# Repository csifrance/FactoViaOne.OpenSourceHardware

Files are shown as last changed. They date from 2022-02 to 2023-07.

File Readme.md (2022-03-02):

# FR : PROMOUVOIR ET FACILITER L’ACCES AUX CONNAISSANCES DE L’INDUSTRIE DU FUTUR, DANS UNE DÉMARCHE D’ÉCONOMIE CIRCULAIRE : LE PROJET "FACTOVIA ONE" A ETE OPEN SOURCE.
# EN : PROMOTE AND FACILITE THE ADOPTION OF THE INDUSTRY 4.0, IN A CIRCULAR WAY : THE "FACTOVIA ONE" PROJECT HAS BEEN OPEN SOURCED.**

## FR: A propos des licences 

Sauf mention contraire, le repositoty a été Open Sourcé au CSI France (Collectif startups industrielles France). L'idée d'origine du projet et l'initiative est attribuée à Vincent Thavonekham. En voici les termes et conditions :
* sur la partie matérielle : [copyright et licence selon la license "Open Source Hardware (OSHW) Définition 1.0"](./LICENSE). 
* sur la partie logicielle : [copyright et licence selon la license "Creative Commons Attribution-ShareAlike 2.0 Generic License" (CC BY-SA 2.0)](./LICENSE-CODE).

Le détail du copyright et des permissions doivent être inclues dans toutes les copies ou portion de code.

Cela signifie en résumé que : 
- vous pouvez librement ré-utiliser le code pour d’autres projets Open Source ou bien des projets commerciaux, tant que vous conservez l’attribution de l’auteur initial.
- vous devez clairement inclure dans le logiciel cette notice sur toutes les copies ou sous-portions de code.
- le code est fournit sans garantie d’aucune sorte.
- les instructions relatives à la partie matérielle vienne sans garantie d’aucune sorte sur d'éventuels préjudices matériel, corporel, moral ou autre.

## EN: About licensing 

Unless otherwise stated, this repository has been made Open Sourced to CSI France (Collectif startups industrielles France) by Vincent Thavonekham, the original creator who has the attribution. Here are the terms and conditions :  
* on the hardware side : [copyright and licence under the term of the "Open Source Hardware (OSHW) Définition 1.0"](./LICENSE). 
* on the software side : [copyright and licence under the term of the "Creative Commons Attribution-ShareAlike 2.0 Generic License" (CC BY-SA 2.0)](./LICENSE-CODE).

This means in summary that :
- you can freely reuse in an open-source application or a commercial application, as long as you keep the original attribution to the original author.
- the above copyright notice and this permission notice shall be included in all copies or substantial portions of the Software.
- the code comes without any warranty of any kind.
- the hardware's instructions comes without no liability for any damage to the hardware, or for personal injury during installation.

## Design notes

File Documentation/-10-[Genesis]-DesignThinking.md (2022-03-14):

# Genesis of FactoVia One and 3 phases of manufactuting R&D : LEGO + Proto + Cardboard 

* Pre-requisites before manufacturinganything ! Market study and Product Market fit
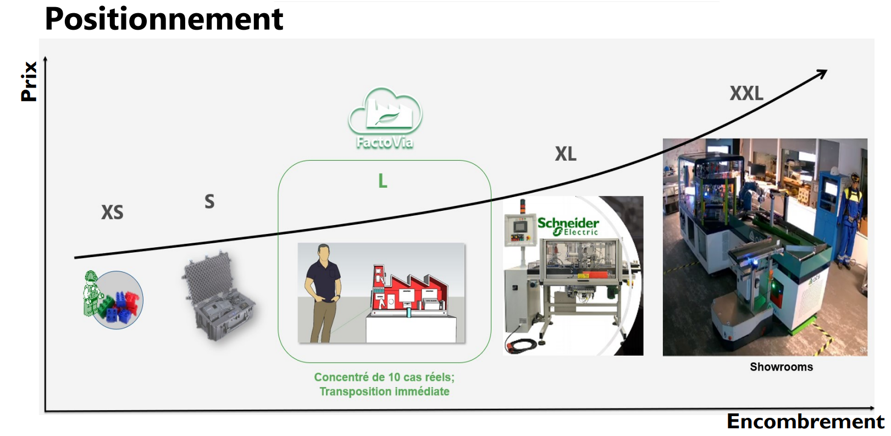
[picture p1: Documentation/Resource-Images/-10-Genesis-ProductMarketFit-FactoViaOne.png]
  * 
  * Work with Montessori Reseacher-Teachers & Psychologues

# LEGO PHASE
* Design with Lego for the color choices and global positionning
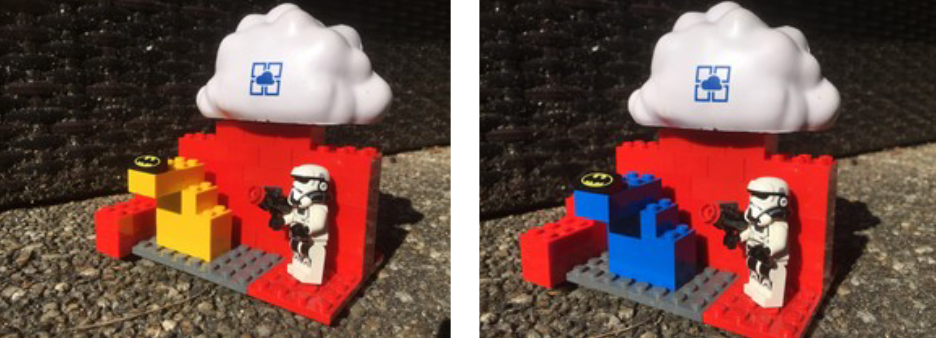
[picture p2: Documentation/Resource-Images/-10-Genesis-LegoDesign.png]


* Testing the conveyor principles with Lego 
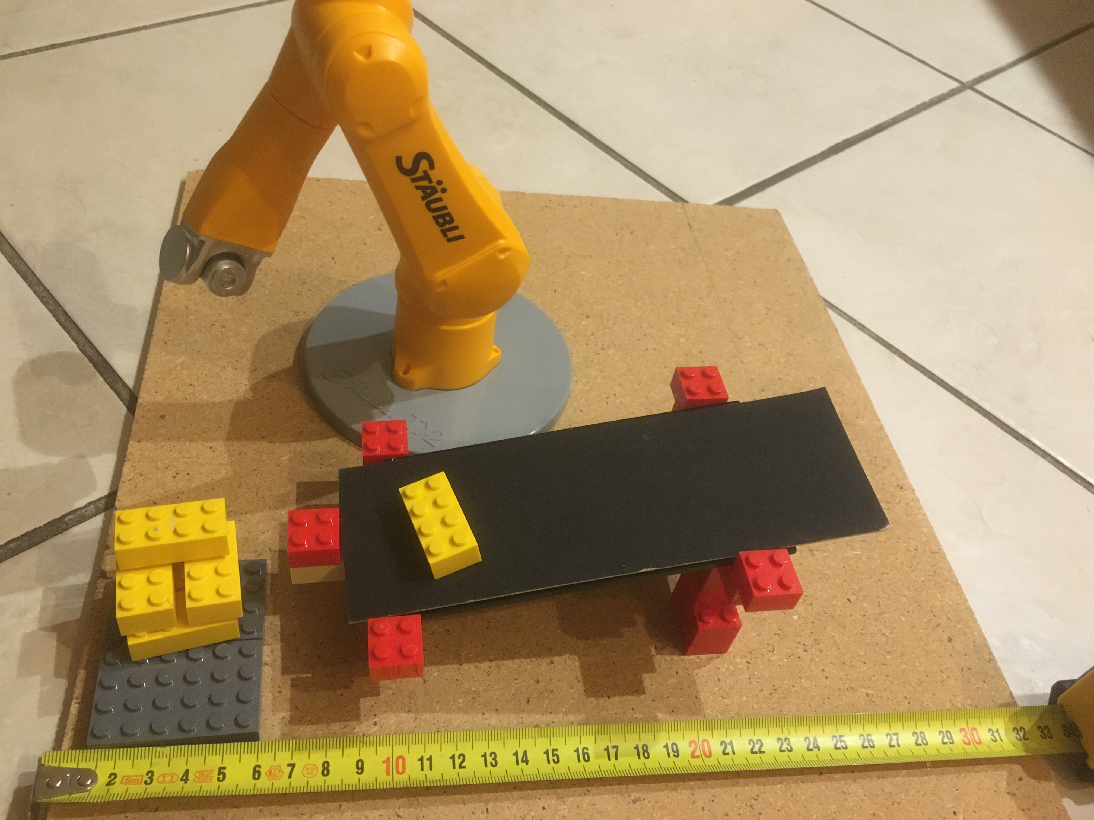
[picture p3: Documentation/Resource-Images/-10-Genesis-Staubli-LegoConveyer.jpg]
 

# MANUFACTUING PHASE
* Cardboard board phase
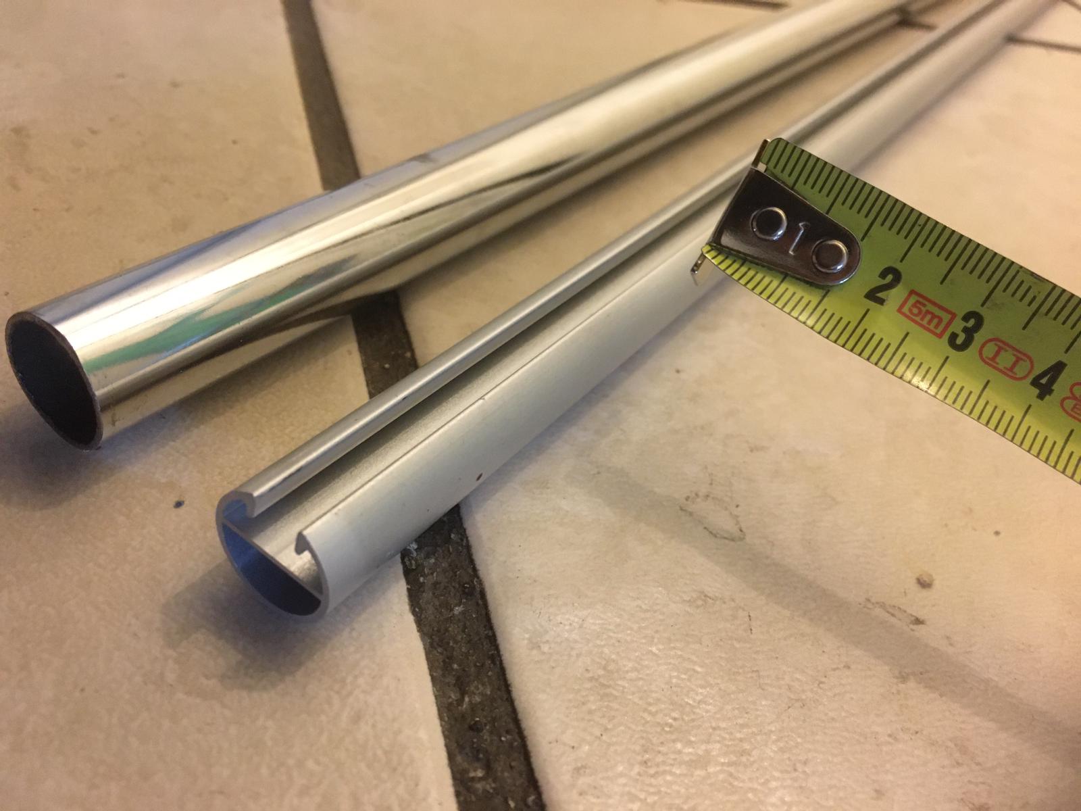
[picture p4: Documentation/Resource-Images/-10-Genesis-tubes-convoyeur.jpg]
 

* Cardboard board phase
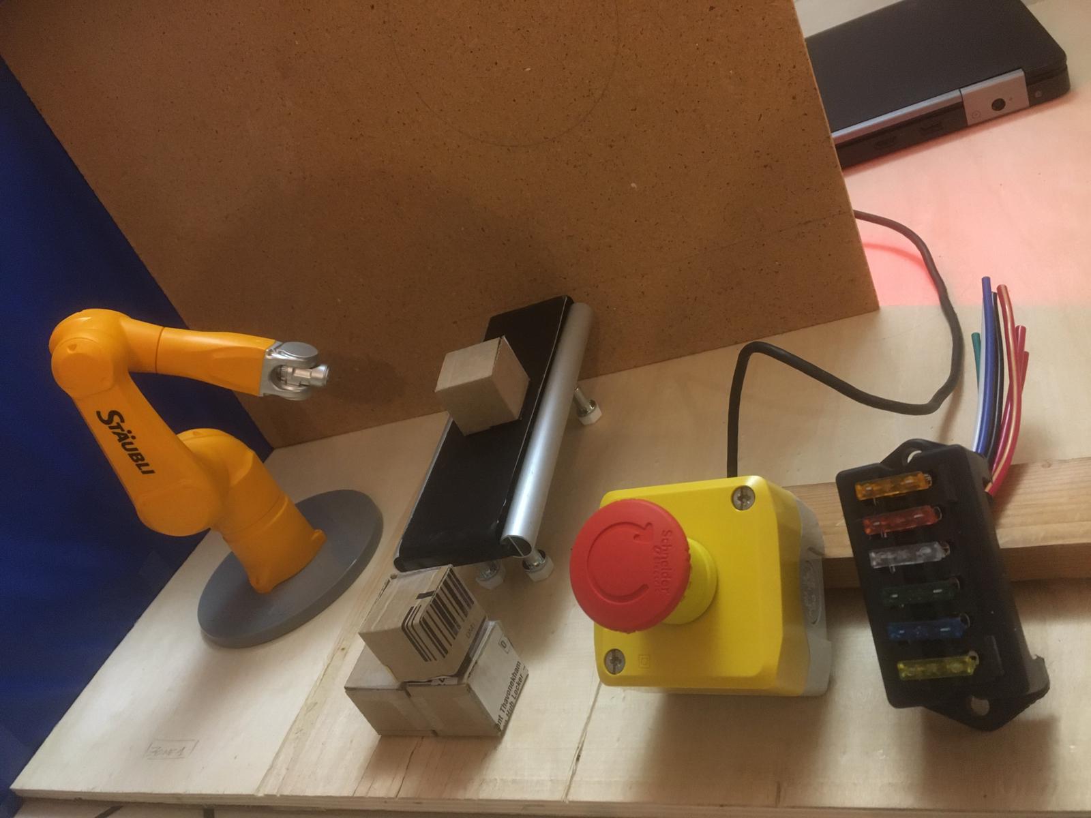
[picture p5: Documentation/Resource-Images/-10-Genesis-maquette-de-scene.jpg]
 

# CARDBOARDBOX PHASE
* Cardboard board phase
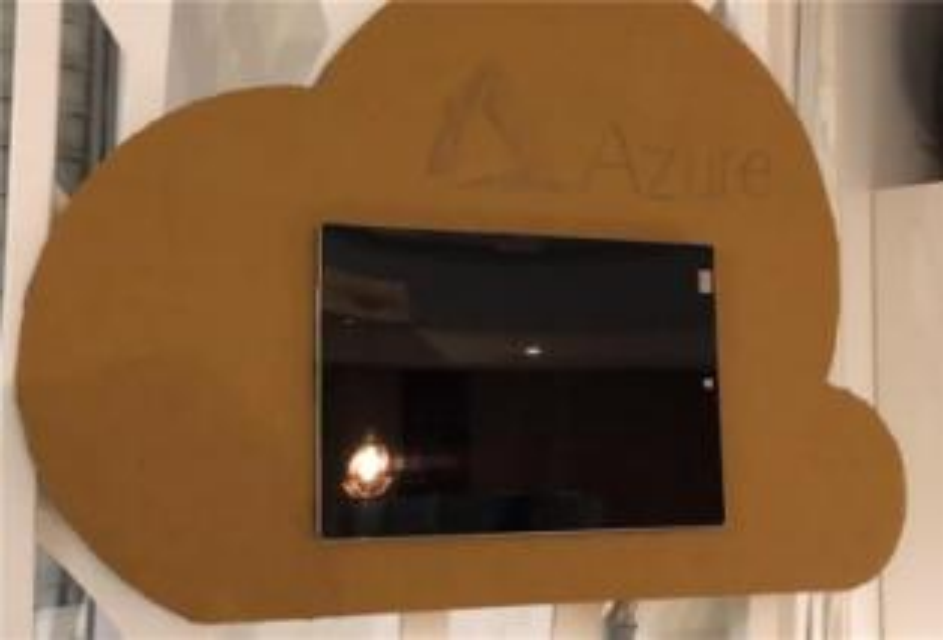
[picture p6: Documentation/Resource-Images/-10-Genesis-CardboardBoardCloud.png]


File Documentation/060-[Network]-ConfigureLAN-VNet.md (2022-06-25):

# Configure LAN and VNet
Now that we have the PLC BB400, the Field gateway and the IoT Edge, we can connect them all to the Switch.

Configuration : 

**PLC BB400**
IP address = 192.168.127.1 (by default; DO NOT CHANGE !)

**Field Gateway - Windows 10**
IP settings = Manual
IP address = 192.168.127.3**
Subnet prefix lenght = 24 
// IPv4 gateway = 192.168.127.1
// IPv4 DNS servers = 192.168.24.254 

**IoT Edge MEVA / HPE - Linux Ubuntu**
* First check current IP address and writ it down
* go to [Top right menu > click on Wifi icon > Click on tool screw driver and wrenk > Network Settings > Network > identify your network (for instance eno1) > click on the right hand-side the wheel icone > Wired > Tab "IPv4" > Ethernet (eno1) > gear_icon > IPv4]
  
IPv4 Method = Manual (as opposed to DHCP)
* address IPv4 = 192.168.127.4
* IPv6 = fe80::3ad5:19f4:1740:b6eb
* H/w address = 00:69:67:D0:04:97
Netmask (try 1 that works to ping : 255.255.0.0)
  * // Subnet prefix lenght = 24 
// Gateway = Leave it blank = cannot be 192.168.127.1 because already used (otherwise always in .1 and the other .2 .3 .4 etc...)
// DNS = leave it automatic ; = 192.168.24.254  ==> Set to default
// Routes = leave it automatic ;

#SANITY CHECK
* From IoT Edge Linux :
  * run ping 192.168.127.1  => time=1.04ms 
  * Ping of itself ! admfactoviaone@iotedge:~/Desktop/Install$ ping 192.168.127.4
     * PING 192.168.127.4 (192.168.127.4) 56(84) bytes of data.
     * 64 bytes from 192.168.127.4: icmp_seq=1 ttl=64 time=0.055 ms
     * 64 bytes from 192.168.127.4: icmp_seq=2 ttl=64 time=0.053 ms
  * Ping of BB400 admfactoviaone@iotedge:~/Desktop/Install$ ping 192.168.127.1
     * PING 192.168.127.1 (192.168.127.1) 56(84) bytes of data.
     * 64 bytes from 192.168.127.1: icmp_seq=1 ttl=64 time=0.648 ms
     * 64 bytes from 192.168.127.1: icmp_seq=2 ttl=64 time=0.844 ms
     * 64 bytes from 192.168.127.1: icmp_seq=3 ttl=64 time=0.875 ms

* From Field Gateway : 
  * run ping 192.168.127.1  => time<1ms TTL=64
  * run ping 192.168.127.3  => time<1ms TTL=128

# TROUBLE SHOOT
* admfactoviaone@iotedge:~/Desktop/Install$ curl 192.168.127.1:9000
curl: (7) Failed to connect to 192.168.127.1 port 9000: Connection refused
  * This may be because your BB400 is rebooting. Try again in 1 or 2 minutes, you should have 
  * admfactoviaone@iotedge:~/Desktop/Install$ curl 192.168.127.1:9000{"io":{"counts":[0,0,0,1,0,0,0,0],"inputs":[1,1,1,1,1,1,1,1],"outputs":[0,0,0,0,0,0,0,0]}}.

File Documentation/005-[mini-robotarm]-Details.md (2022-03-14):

# Details of the mini-dummy robot arm

This robot arm came mostly from a gift from Stäubli, and then customized for its cirle metallic bases

* **Hight** (arm deployed) = 265 mm
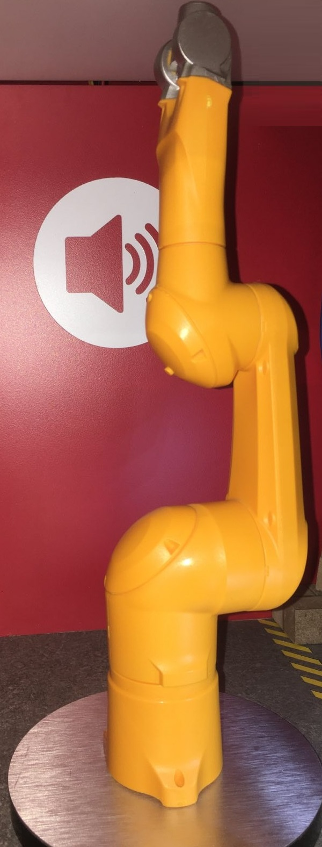
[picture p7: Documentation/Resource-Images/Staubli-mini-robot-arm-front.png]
  * 

* **Width** 
  * Width (metallic circle base) = 100 mm
  * Width (robot base) = 40 mm
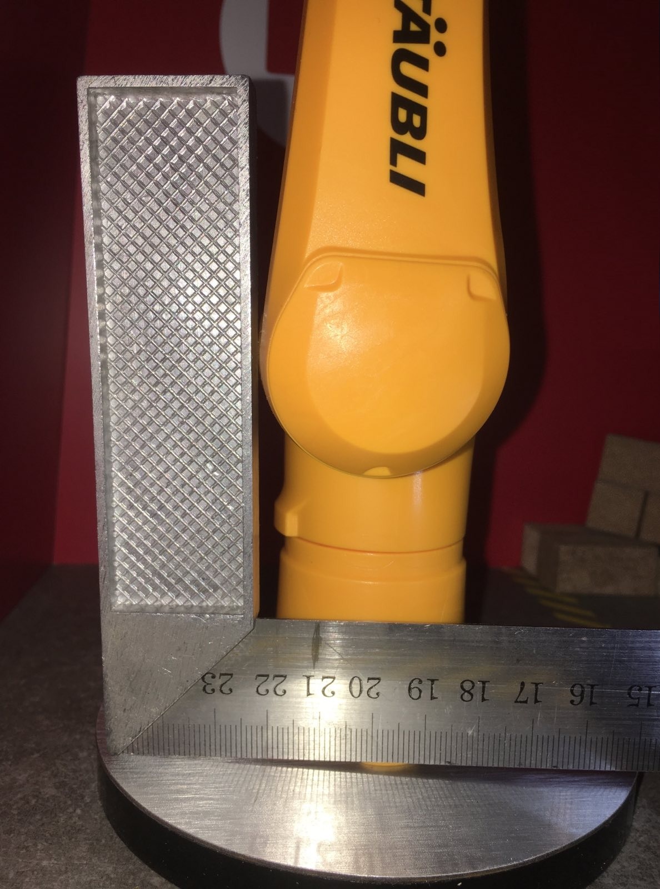
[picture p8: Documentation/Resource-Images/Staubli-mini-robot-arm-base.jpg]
  * 

* You could also print your own
  * use for example the exported TinkerCAD model into Mini-robotarm-NR-UR-Model1.obj and Mini-robotarm-NR-UR-Model1.stl (see folder ./Resource-3D-plan). Here with the printer Creator Pro with a base of 227 x 148 x 150.
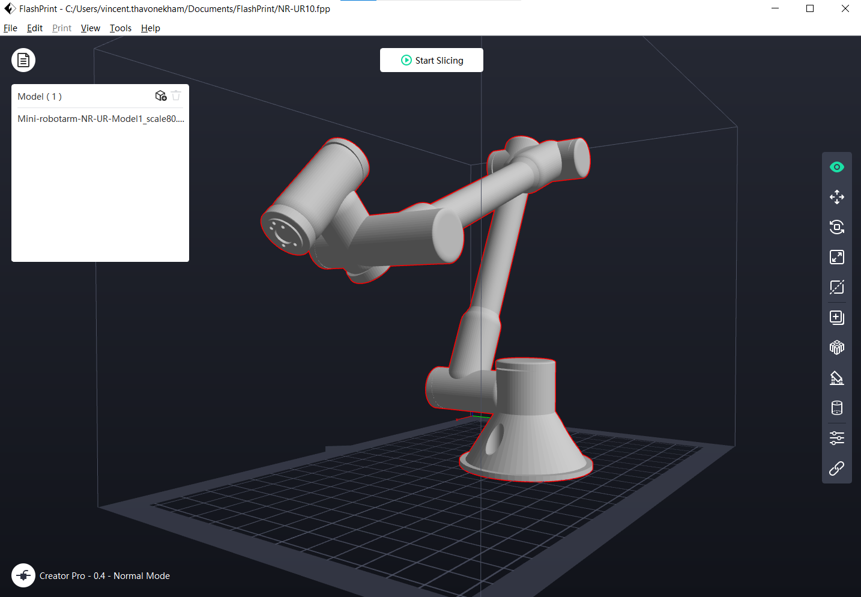
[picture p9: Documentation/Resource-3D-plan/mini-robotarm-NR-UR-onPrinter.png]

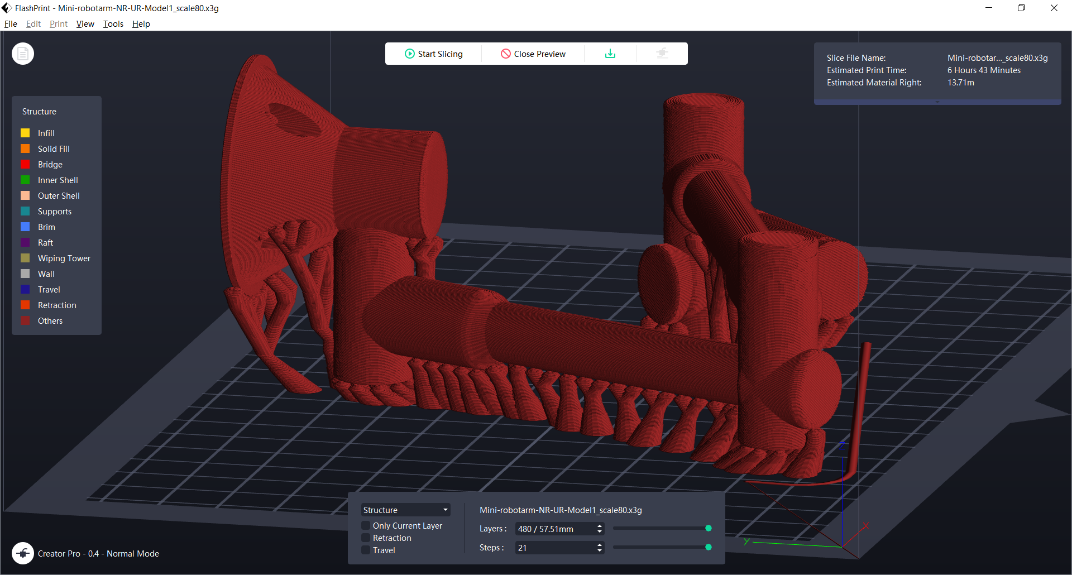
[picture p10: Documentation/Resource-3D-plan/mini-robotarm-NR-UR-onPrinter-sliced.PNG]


The source of the original Creative Commons 3D source file (AUTODESK(R) TinkerCAD(R)) is : https://www.tinkercad.com/things/4TjY5777QWU  
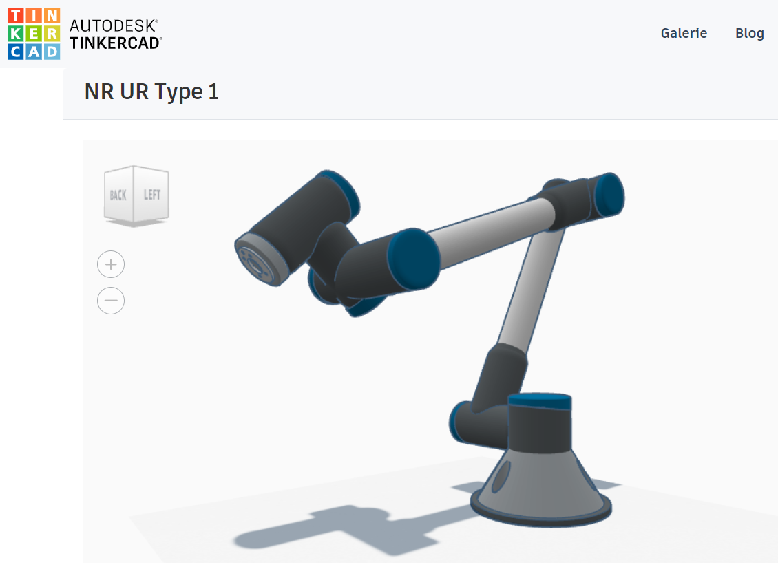
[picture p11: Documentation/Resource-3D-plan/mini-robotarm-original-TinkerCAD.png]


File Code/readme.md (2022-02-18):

FR : Ce fichier présente la liste des différents code source, explique comment les utiliser et leurs liens.

EN : This file presents the list of the various source code, explaines how to use them, and how they relate.

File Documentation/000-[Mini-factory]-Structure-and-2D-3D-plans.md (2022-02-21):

**Mini-Factory Structure**

FR : Exemple de mini-usine. Parce que cela n'est qu'une coquille, vous pouvez soit la recréer, voit créer votre propre design.

EN : Example of the mini-factory. Because, it is only a shell, you could either respect the following dimensions or create you onw one.

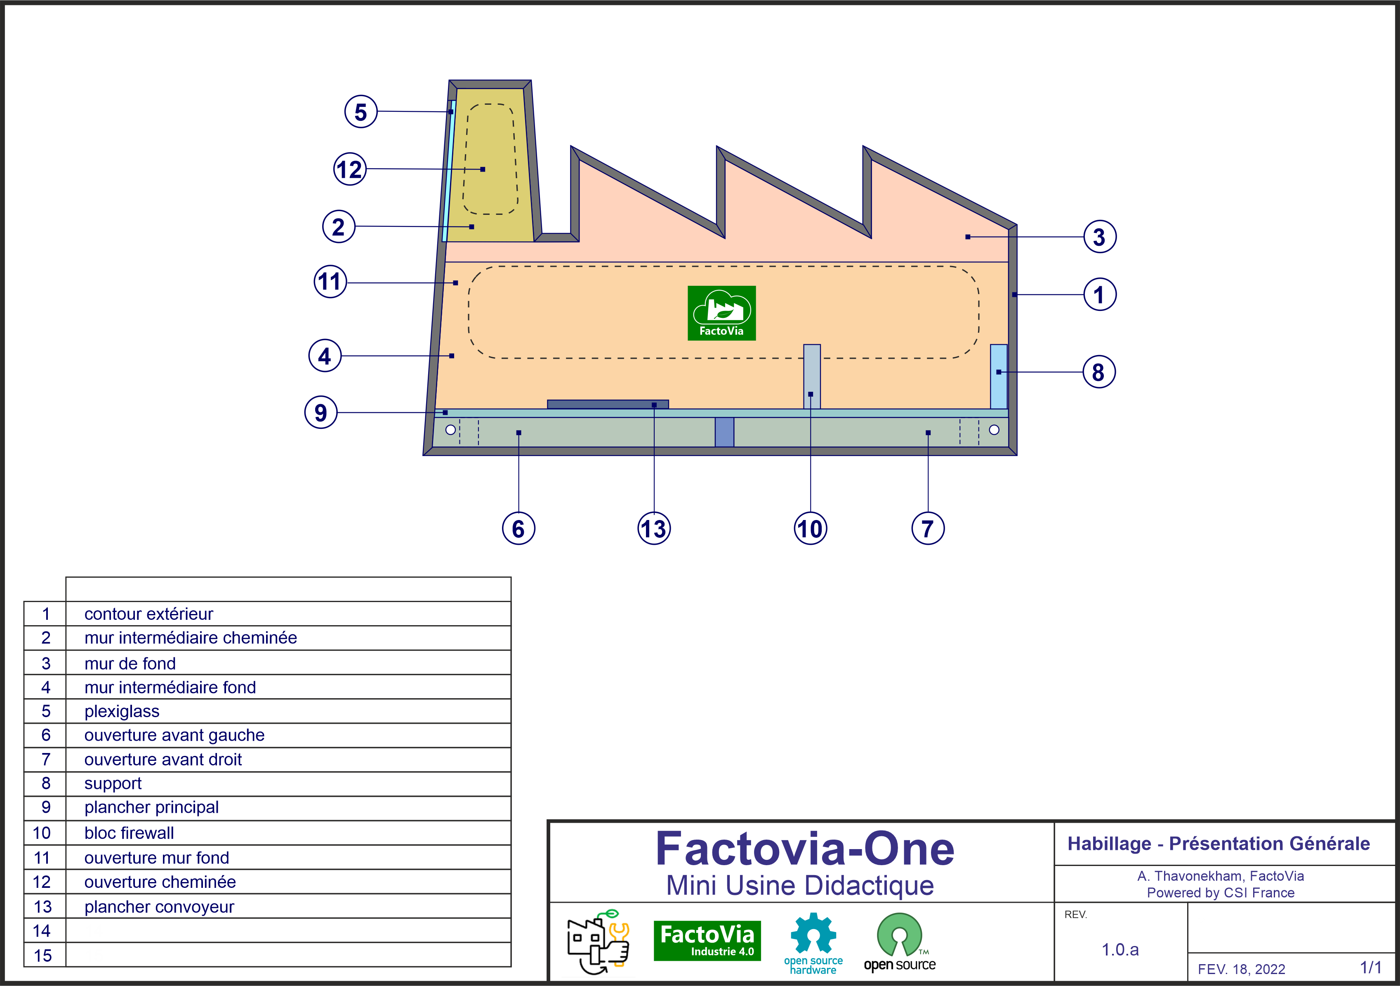
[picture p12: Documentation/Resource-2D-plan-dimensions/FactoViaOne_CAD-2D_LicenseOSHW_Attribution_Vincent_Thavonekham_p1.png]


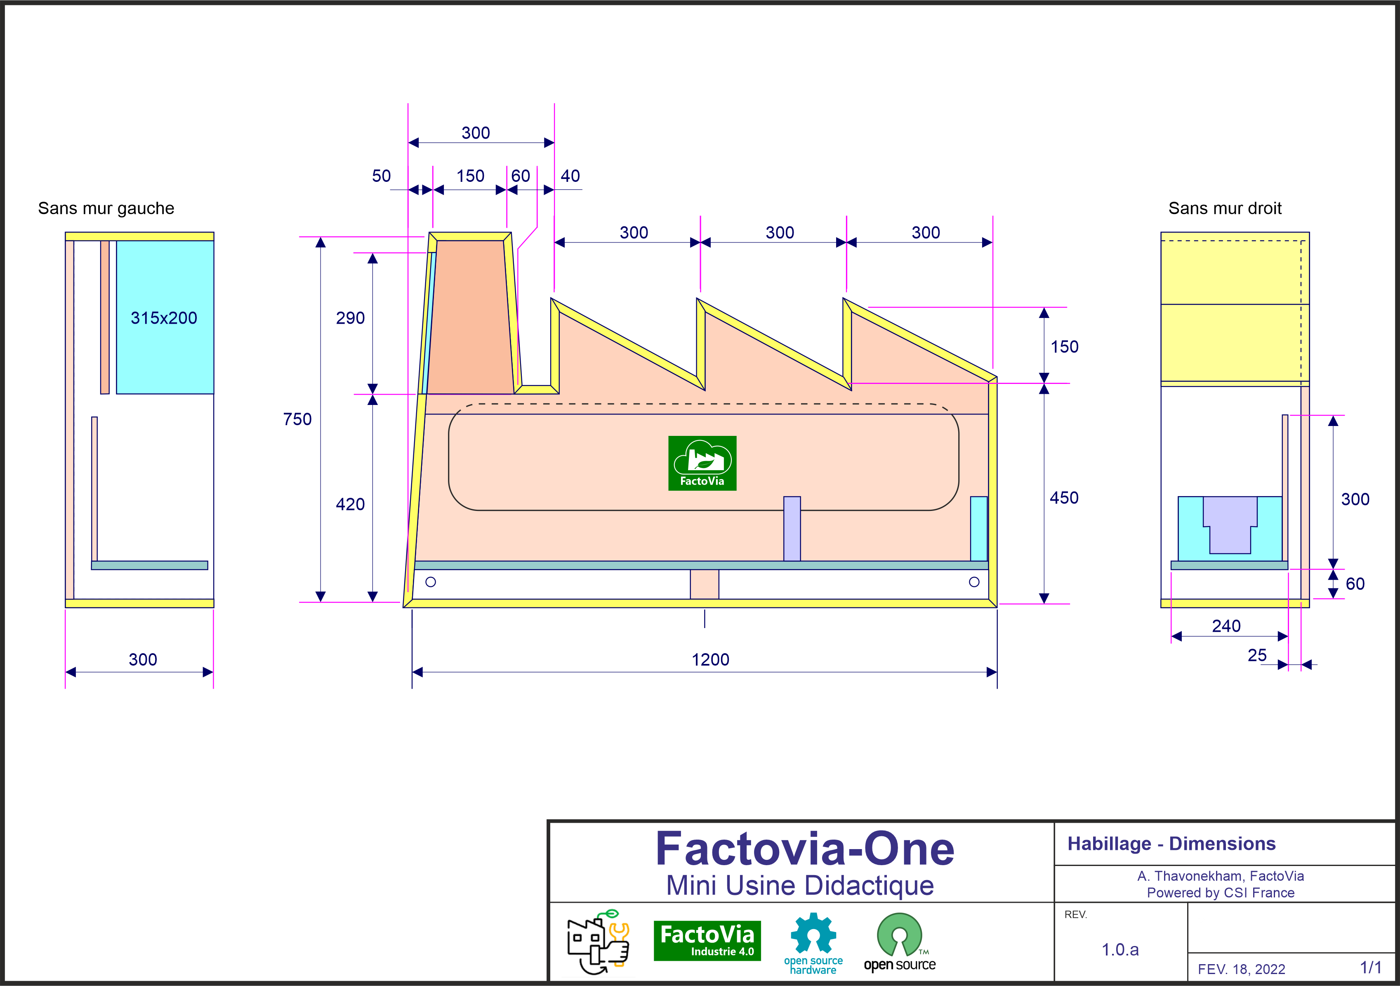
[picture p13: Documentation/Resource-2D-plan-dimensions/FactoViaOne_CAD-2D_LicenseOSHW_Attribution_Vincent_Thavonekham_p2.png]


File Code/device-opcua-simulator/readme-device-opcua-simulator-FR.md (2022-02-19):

FR : Ce simulateur d'objet connecté va s'appuyer sur un véritable **code en production **sachant gérer le standard industriel OPC UA. Nous allons nous appuyer sur le projet [Open Source NodeOPCUA](https://node-opcua.github.io) de sterfive.com

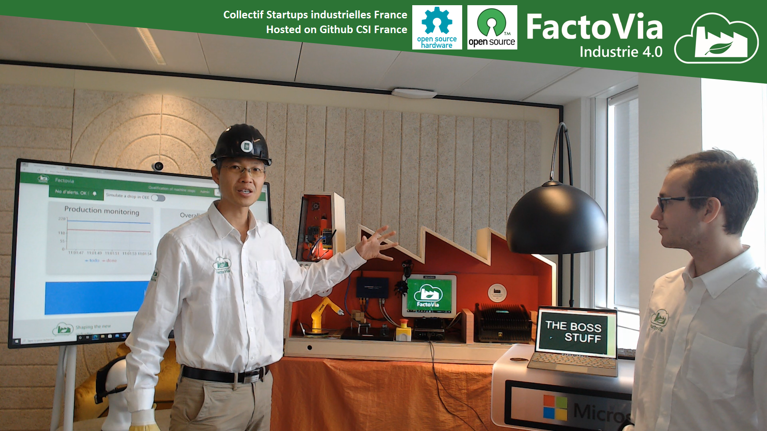
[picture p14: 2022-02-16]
Spash_OpenSource_CSIFrance_FactoVia.png

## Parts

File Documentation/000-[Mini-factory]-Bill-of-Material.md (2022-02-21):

# What's needed to create a FactoVia One mini factory ??

Indication of price : save a minimum of about 10 000$ to perform such project
Indication of timeline

The minimum needed for the FactoVia Core Open Source are the following : 

HARDWARE 
* **IoT-Edge box** : Either HPE EL300, or the Arestech MEVA-3110
  * Idea of price range : 2000$ to 5000$
  * https://buy.hpe.com/us/en/servers/edgeline-systems/edgeline-systems/edgeline-converged-edge-systems/hpe-edgeline-el300-converged-edge-system/p/1011127891  
  * https://www.arestech.com.tw/machine-vision-computer-meva-3110.html
* **protocol converter gateway** : ADVANTECH ARK-1124 U 
  * Idea of price range : 600$ to 800$
  * https://www.advantech.com/products/1-2jkbyz/ark-1124u/mod_e4faa6eb-0cd1-4c55-b2d9-0dea6c8cbdff 
* **PLC or Field-Edge** : Brainboxes BB-400
  * Idea of price range : 500$ to 700$ 
*  **Tactile Industrial Monitor VGA/HDMI/DVI**
   *  Idea of price range : 500$ to 1200$

* **Industrial Tower-light 3-colors** : Schneider Electric Harmony (Green Premium(TM))
  * Idea of price range : 300$ to 400$

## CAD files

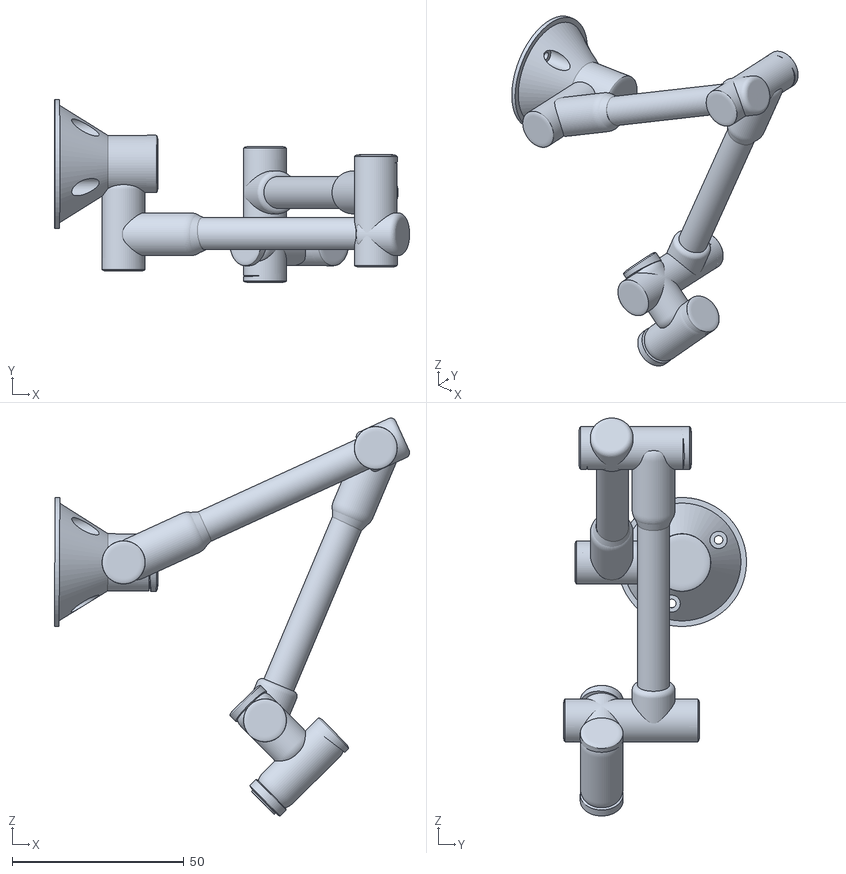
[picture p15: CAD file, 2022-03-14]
Documentation/Resource-3D-plan/Mini-robotarm-NR-UR-Model1_scale80.obj
103.5 x 53.3 x 115.9

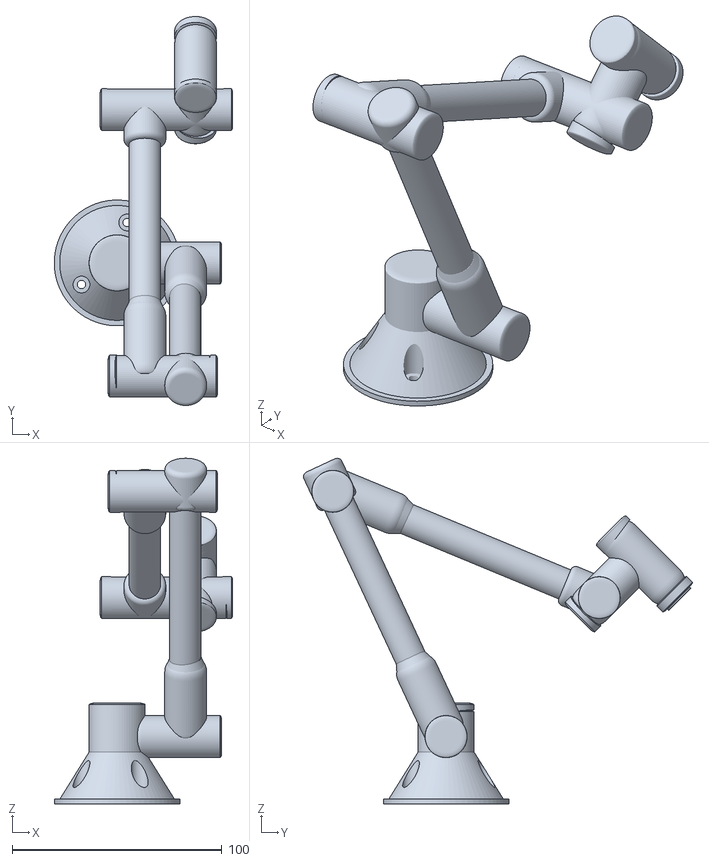
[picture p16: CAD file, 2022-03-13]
Documentation/Resource-3D-plan/Mini-robotarm-NR-UR-Model1.stl
85.1 x 185.5 x 164.8

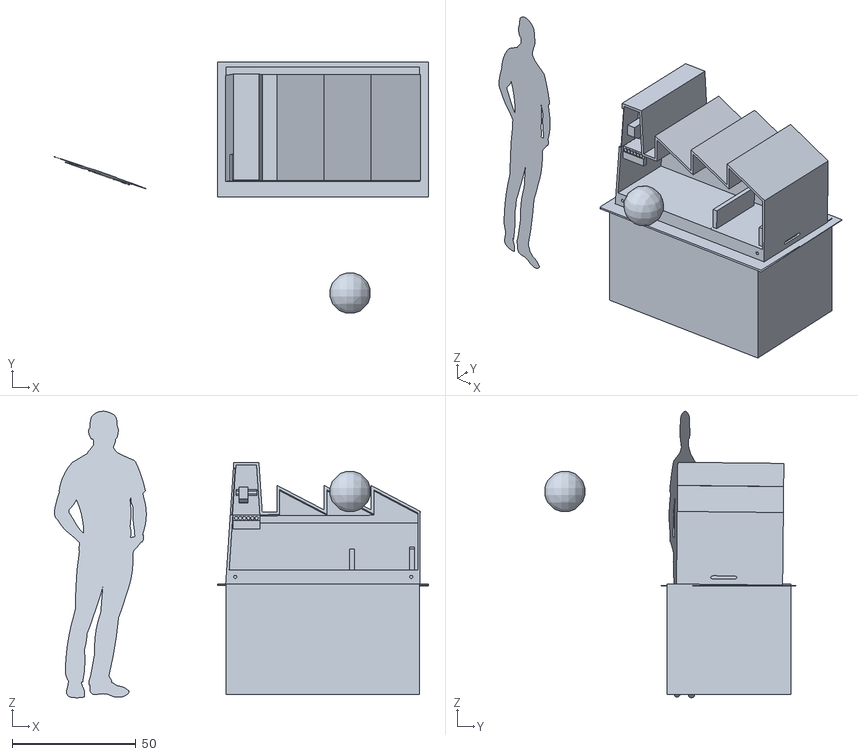
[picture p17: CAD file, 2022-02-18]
Documentation/Resource-3D-plan/FactoViaOne_CAD_3D_LicenseOSHW_Attribution_Vincent_Thavonekham.stl
150.9 x 101.4 x 115.6

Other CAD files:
Documentation/Resource-3D-plan/Mini-robotarm-NR-UR-Model1.obj
Documentation/Resource-3D-plan/Mini-robotarm-NR-UR-Model1_scale80.blend

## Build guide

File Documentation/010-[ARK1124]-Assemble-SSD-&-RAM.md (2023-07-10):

**Assemble your own ADVANTECH ARK-1124 : PART 1 - add SSD **

BILL OF MATERIAL : search for ADVANTECH ARK-1124U
For example : 
https://www.advantech.com/products/1-2jkbyz/ark-1124u/mod_e4faa6eb-0cd1-4c55-b2d9-0dea6c8cbdff

In the case below, if you are an advanced user, we are detailing the assembly for your own specification (else you could buy it off the shelf with everything already mounted).
A grounded anti-static mat and a wrist strap are recommended for your work area
* ensure you are wired to Ground of the ARK-1124 with wrist strap
you have many versions of bracelets / wrist strap, for example an traditional green one, 

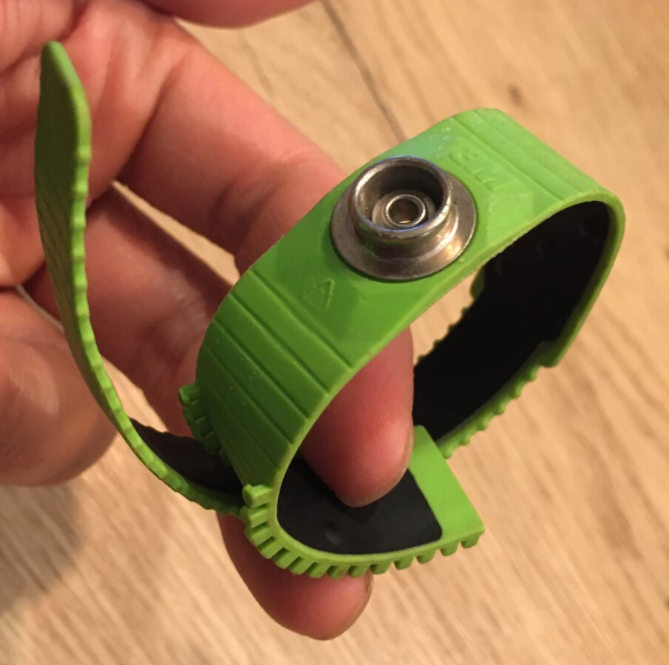
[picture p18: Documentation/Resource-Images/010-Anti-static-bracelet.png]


* or a home-made one by recycling old goodies

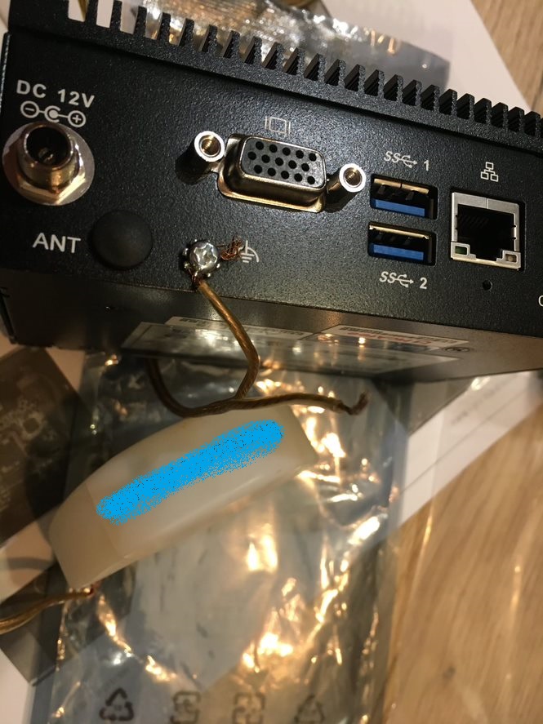
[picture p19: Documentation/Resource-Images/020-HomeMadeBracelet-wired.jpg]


* for example : your arm :

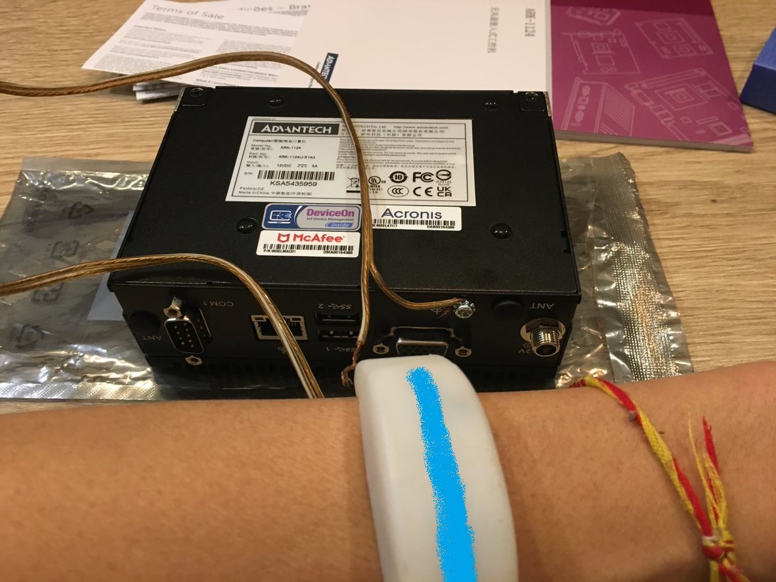
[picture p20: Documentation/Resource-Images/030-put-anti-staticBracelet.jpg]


* To install SSD, unscrew 4 screws of the bottom
  
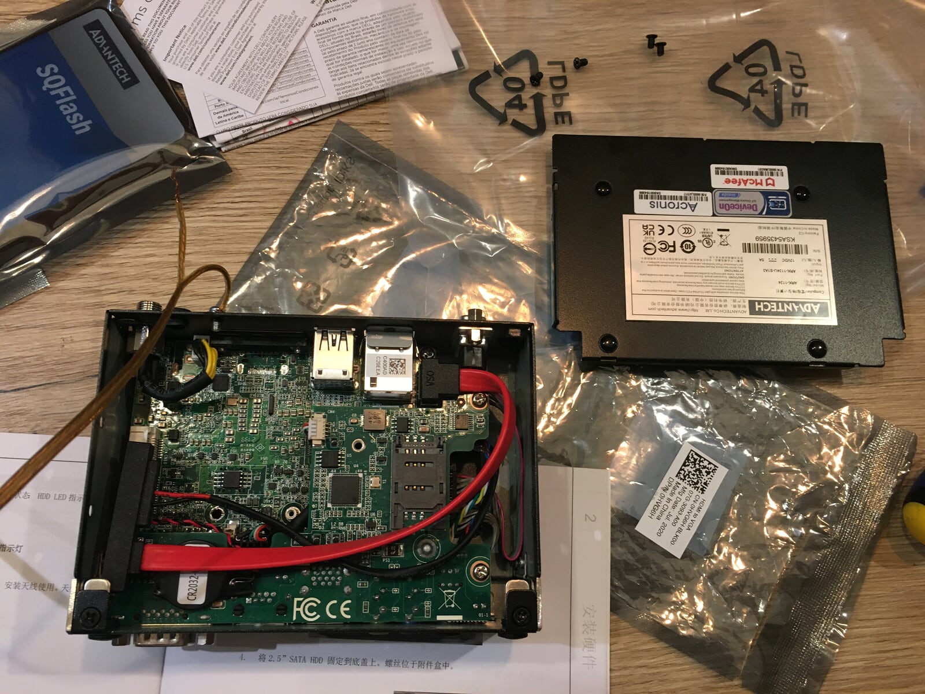
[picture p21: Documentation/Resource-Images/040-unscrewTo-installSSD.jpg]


* You can notice a slot to extand with 4G SIM card
  
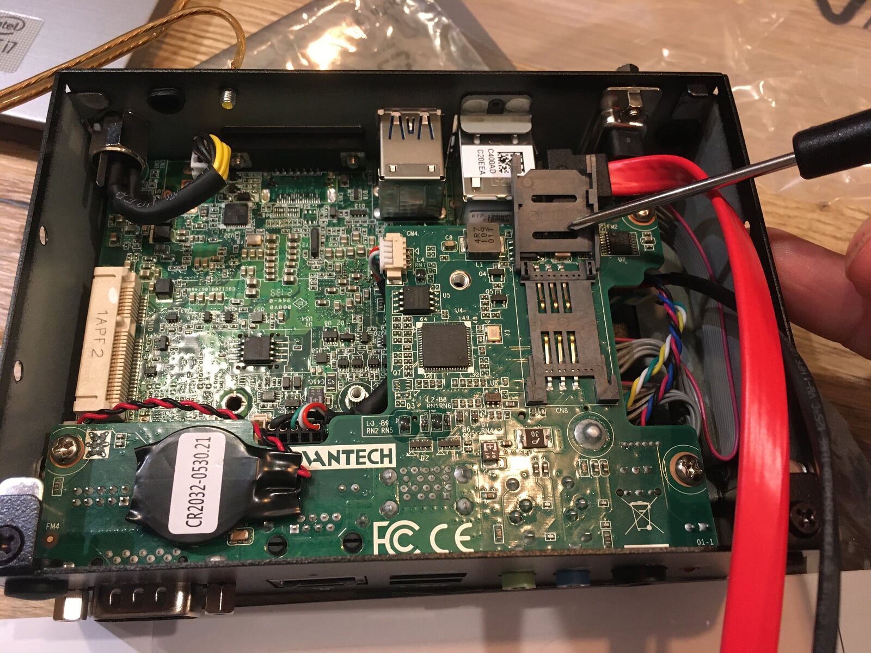
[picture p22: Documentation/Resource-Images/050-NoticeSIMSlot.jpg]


* Rotate the SSD on the correct position to plug the cables
  
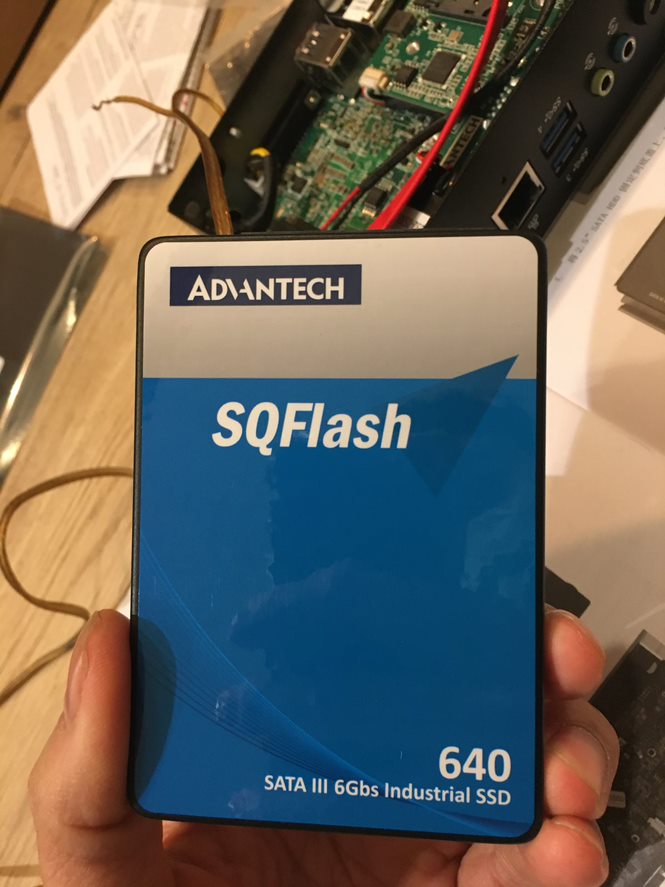
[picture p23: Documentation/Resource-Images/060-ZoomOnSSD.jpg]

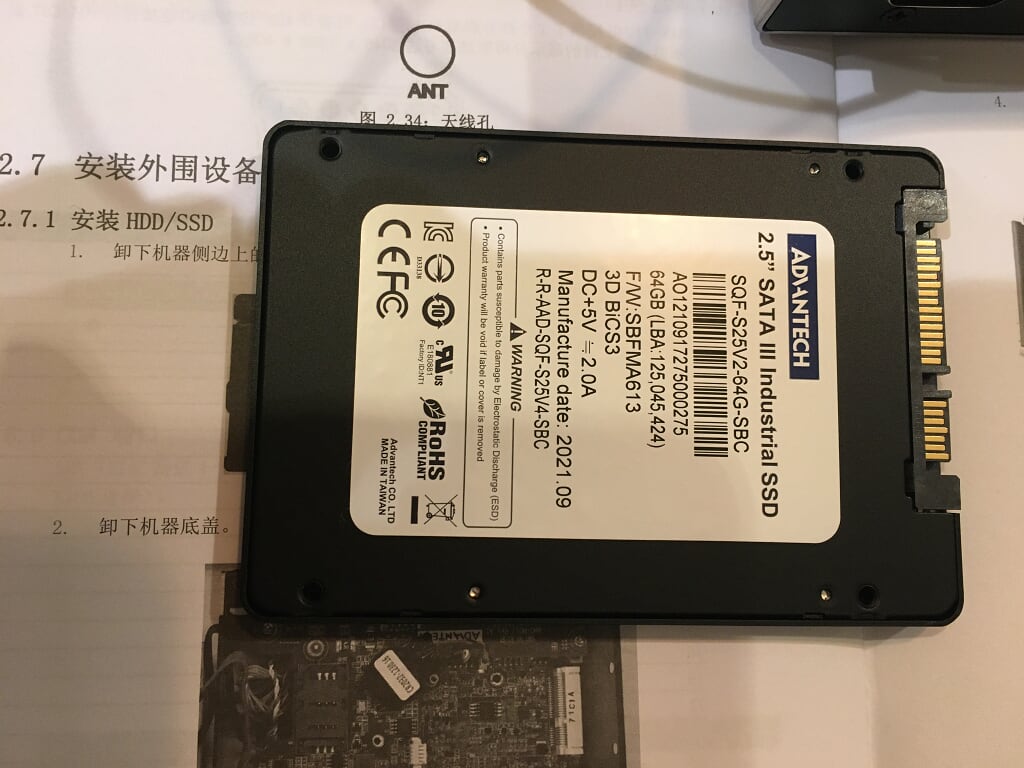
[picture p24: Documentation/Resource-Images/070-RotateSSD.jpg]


* once plugged it should look like this
  
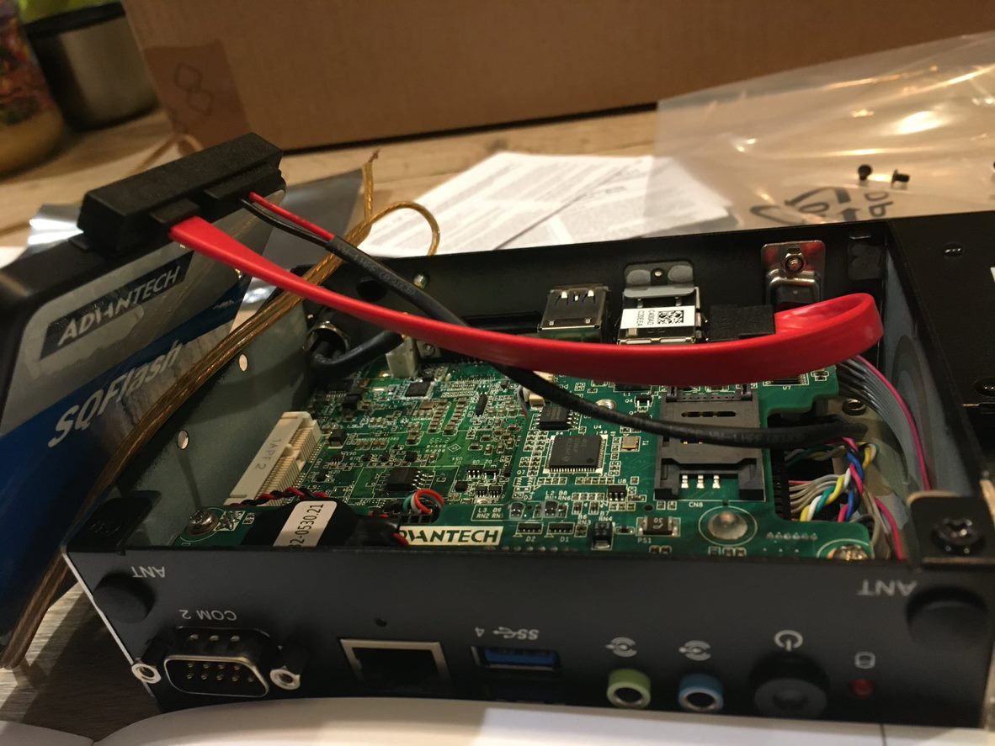
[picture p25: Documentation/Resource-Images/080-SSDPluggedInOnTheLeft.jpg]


* from the metallic plate, remove the 4 tiny pins that will be replaced by the screws
  
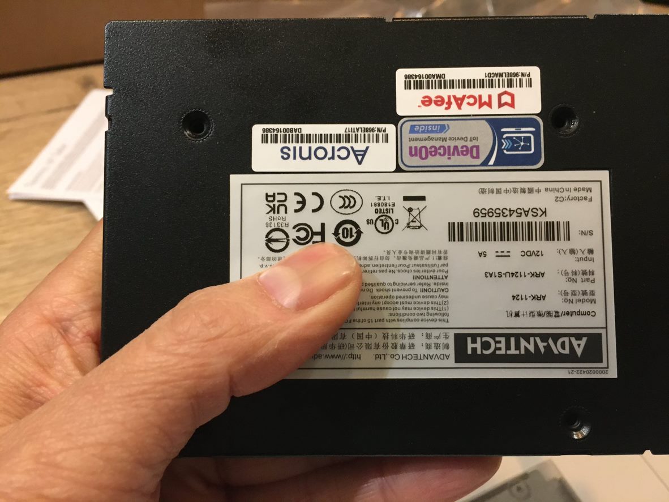
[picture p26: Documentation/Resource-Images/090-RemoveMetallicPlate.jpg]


* attach the SSD and screw the 4 screws, and put the 4 tiny pins back into the plastic bag
  
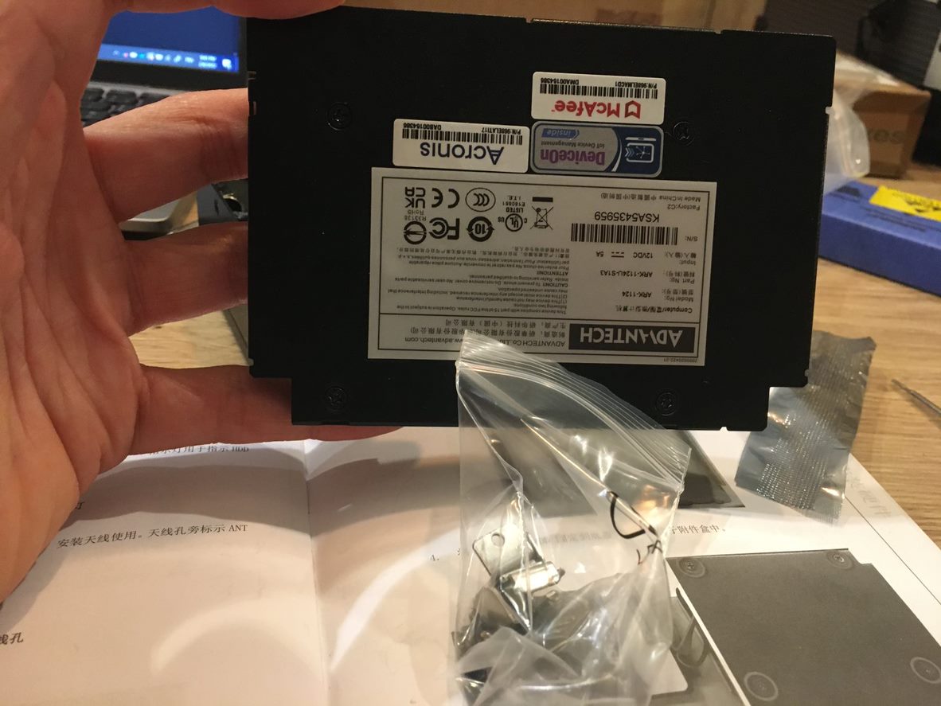
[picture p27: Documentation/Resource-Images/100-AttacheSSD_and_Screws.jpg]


**Assemble & configure your own ADVANTECH ARK-1124 : PART 2 - add RAM **
* prepare the Bill of material
  
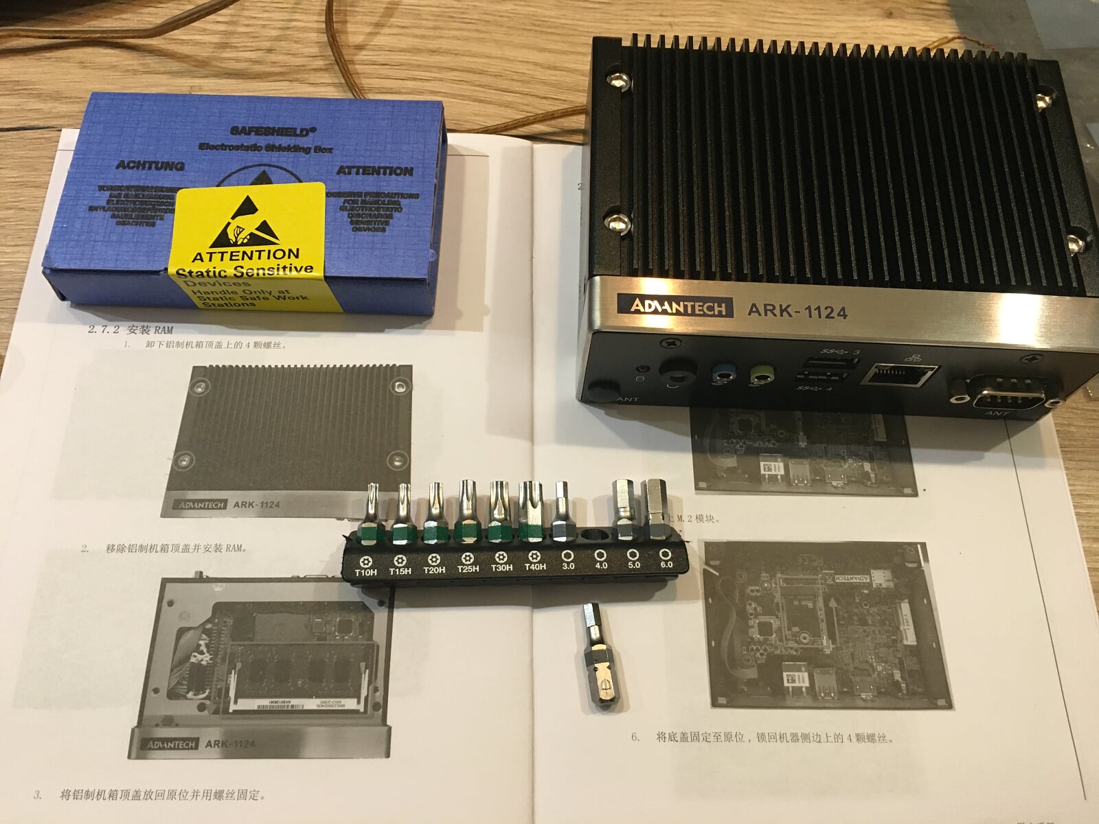
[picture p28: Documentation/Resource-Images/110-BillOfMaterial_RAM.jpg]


* unscrew the 4 screws
/!\ DANGER 1 : Ensure your arm is still being wired to the Ground of the ARK-1124
**/!\ DANGER 2 : When removing the heater by unscrewing the 4 screws, YOU NEED TO BE REALLY CAREFULL about the CPU and the surrounding electronical componants where special heating paste and foam are present. DON'T TOUCH THEM, DONT'T REMOVE THEM. Else the fanless system will fail, and your ARK-1124 will overheat and be damaged !***
(1) small black square foam insulation on the left of the CPU
(2) larger black rectangle foam insulation that will go on the top of the RAM, once inserted (see operations after)
(3) medium black square foam insulation on the right of the CPU. I removed carefully to take a picture of the electrical components circled in orange to show you what it underneath
(4) blue heat transmitter paste that conducts the heat from the CPU to the large heater plate

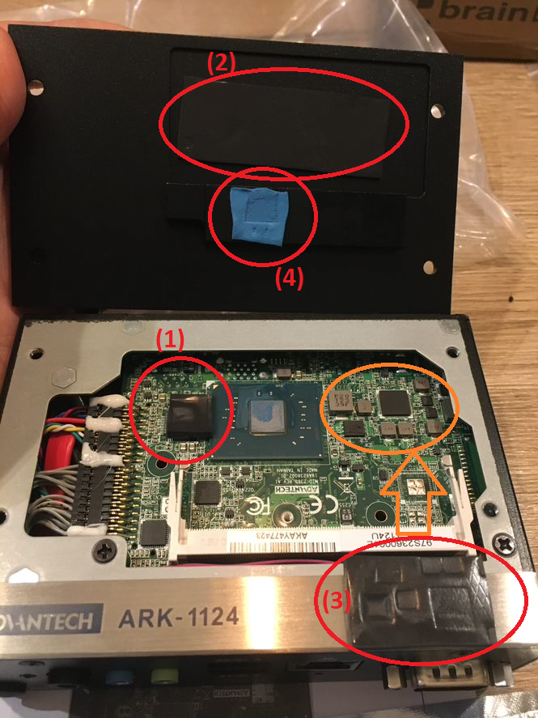
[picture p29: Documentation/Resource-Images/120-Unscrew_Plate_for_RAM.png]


* Prepare the RAM
  
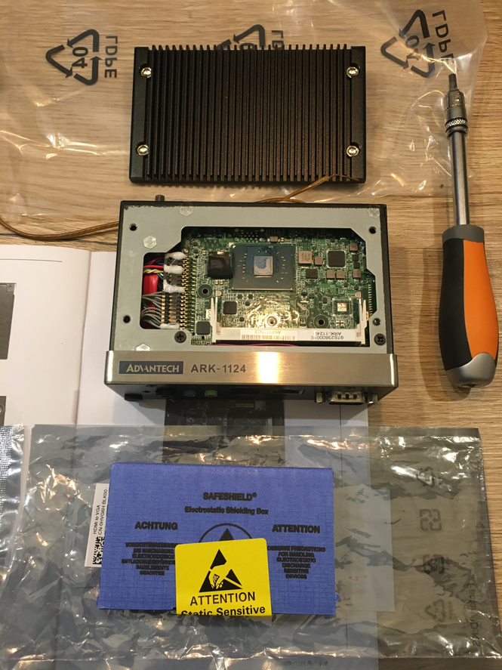
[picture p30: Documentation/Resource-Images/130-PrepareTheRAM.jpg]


* Again, ensure that your arm is really shilded to the Ground of the ARK-1124 because of the static sensitive nature of what we are doing.
 Then un pack the RAM

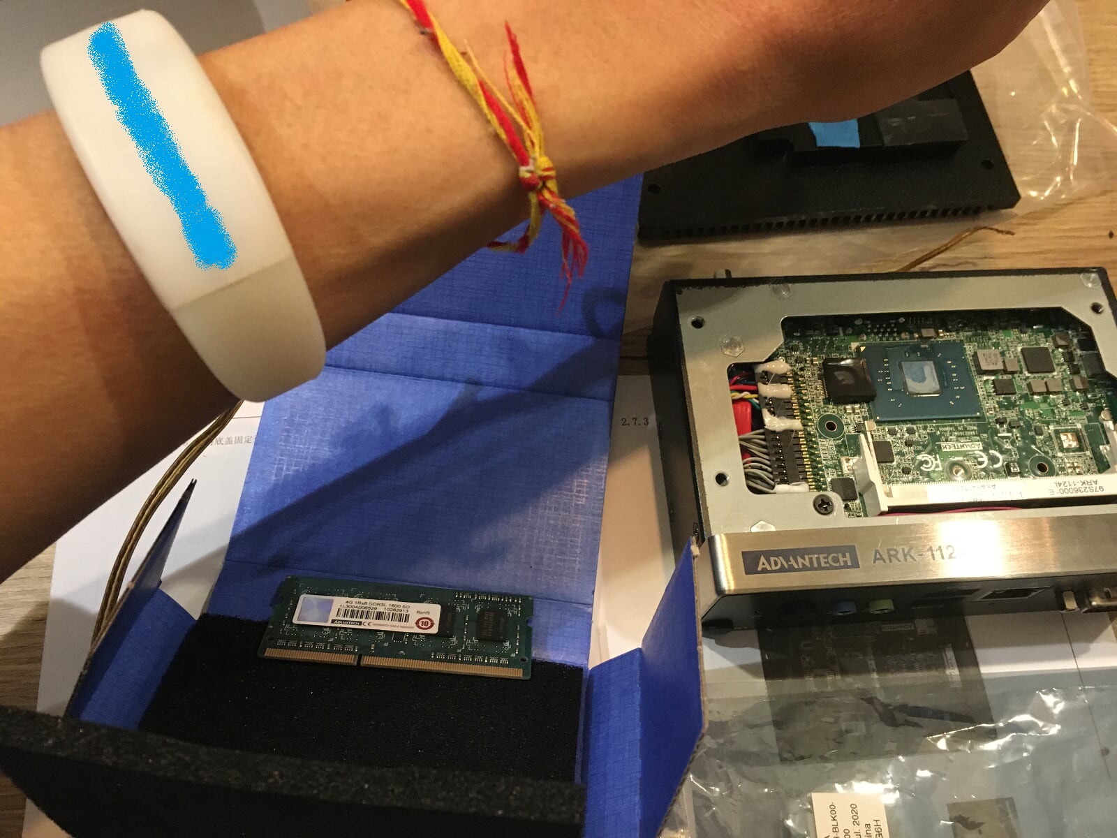
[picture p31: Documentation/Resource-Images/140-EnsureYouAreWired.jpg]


* insert in the angle shown below. DO NOT TOUCH THE PINS (it could rust) & DO NOT TOUCH ANY COMPONENTS !!! Just the edge of the RAM.
  
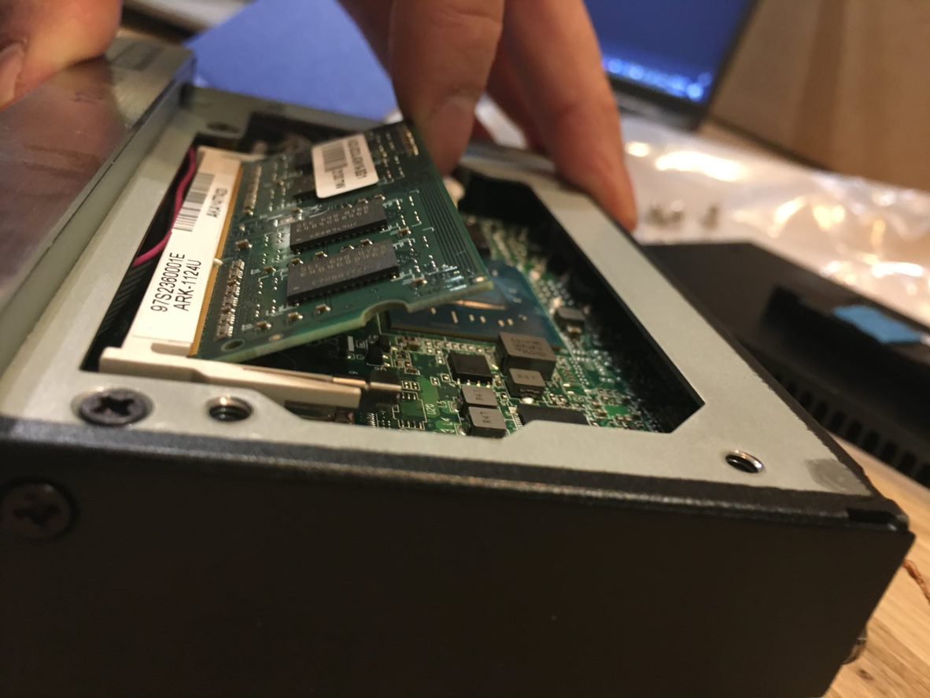
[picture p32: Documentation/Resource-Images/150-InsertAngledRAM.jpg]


* push the RAM into horizontal position to suppress the initial angle. Ensure the left and right semi-metallic circle blocking systems are in place in the semi-circle cut of Circuit board of the RAM (Note : the semi-metalic circle are not exactly aligned with the slot)
  
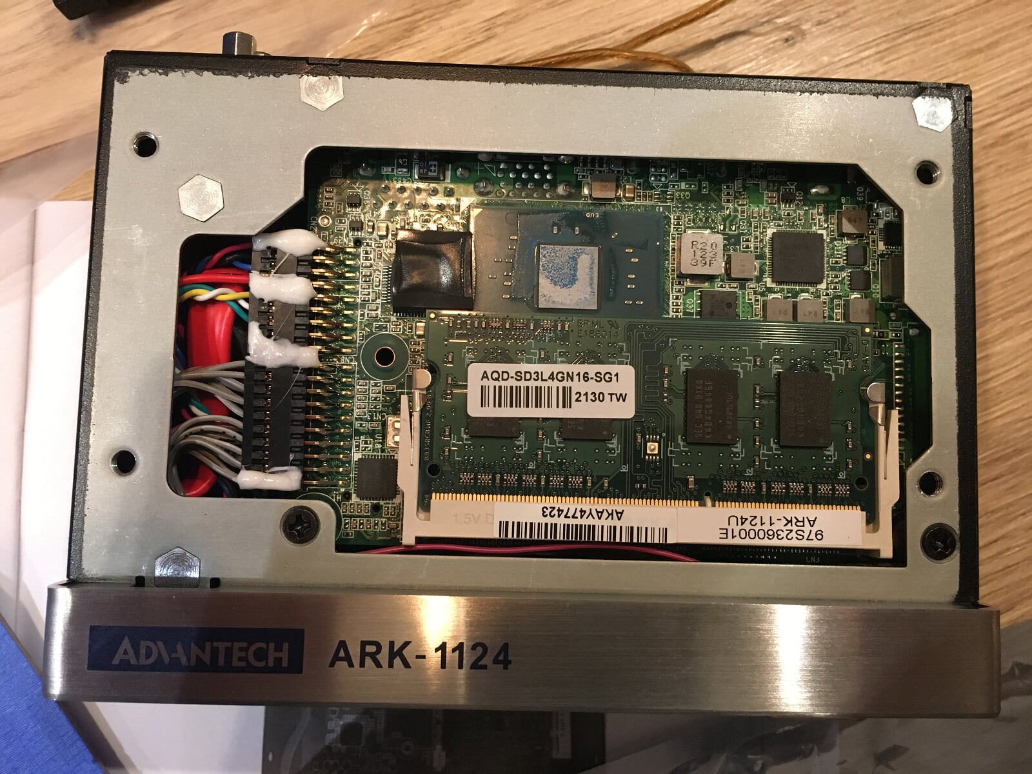
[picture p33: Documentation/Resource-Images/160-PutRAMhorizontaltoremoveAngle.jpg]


* Reshape the Bleu-heat conduction paste before closing the box. For that, because the blue-heat-conduction that goes on top of the CPU has been flattened, you need to carfully reshape it, to ensure optimum heat conduction
  
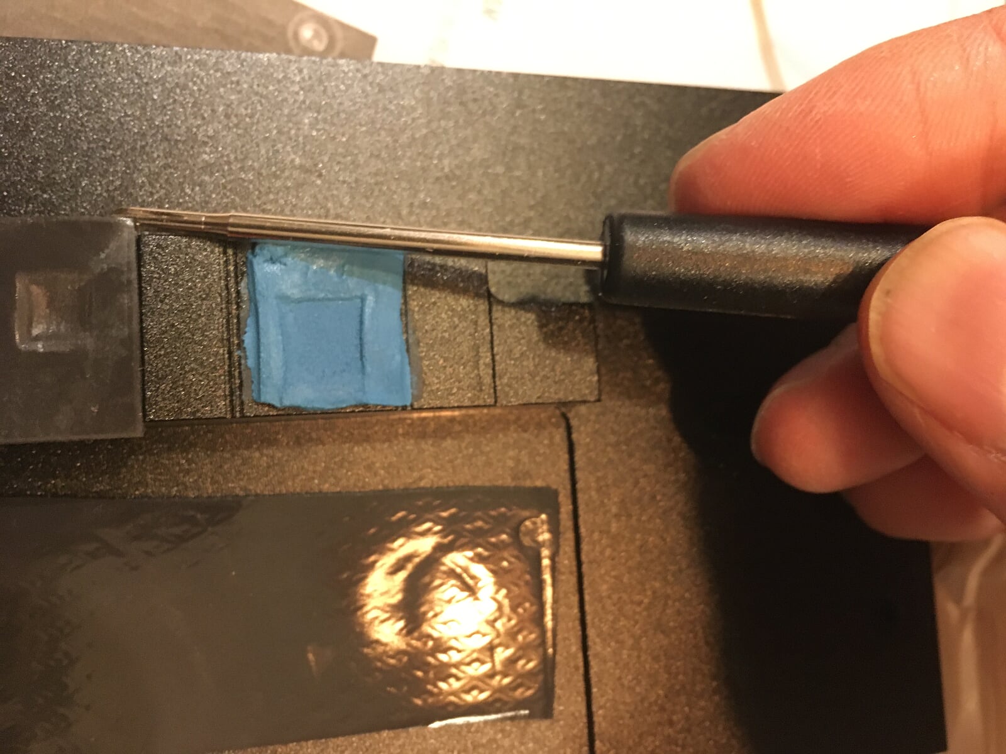
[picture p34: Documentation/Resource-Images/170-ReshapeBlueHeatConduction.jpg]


* close and screw back

* **SANITY CHECK :** 
* plug the electricity => Orange light
* Turn on (press the Orange light) => Green light + Beep (x4)
  
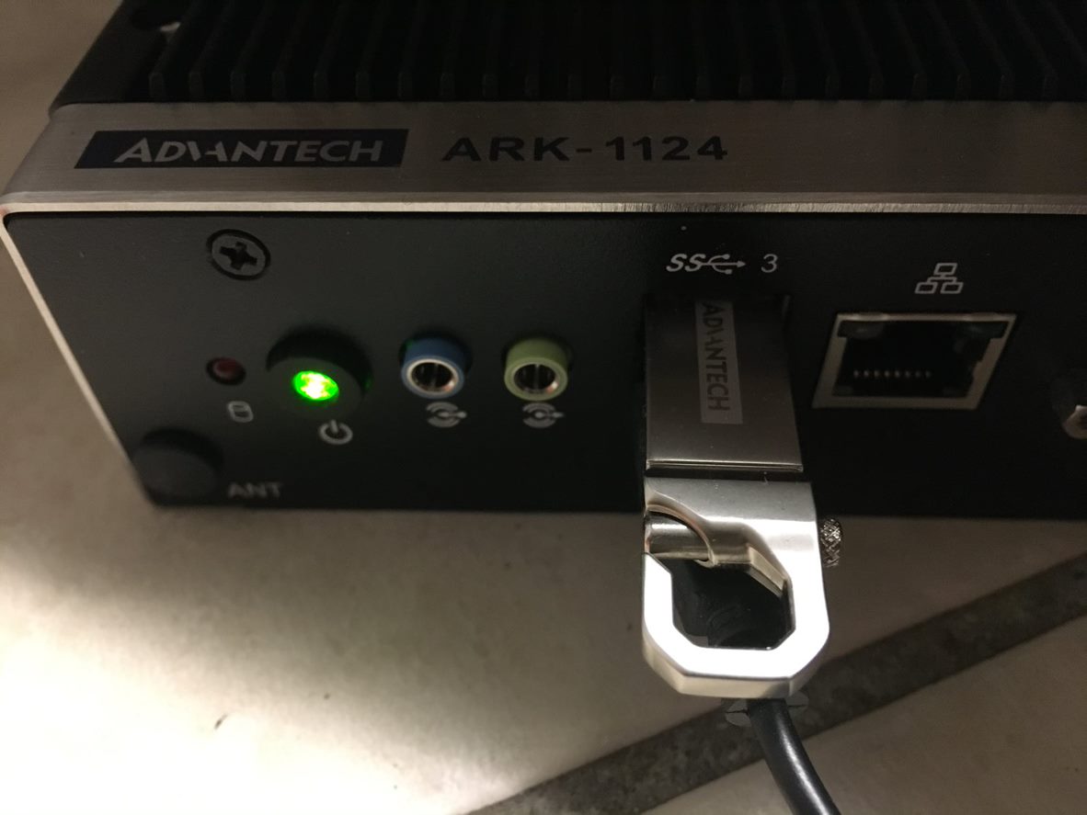
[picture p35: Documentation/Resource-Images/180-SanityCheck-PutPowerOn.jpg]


* start the install of the OS process (below), and the SSD should be read/writing, and generated flashy red lights
  
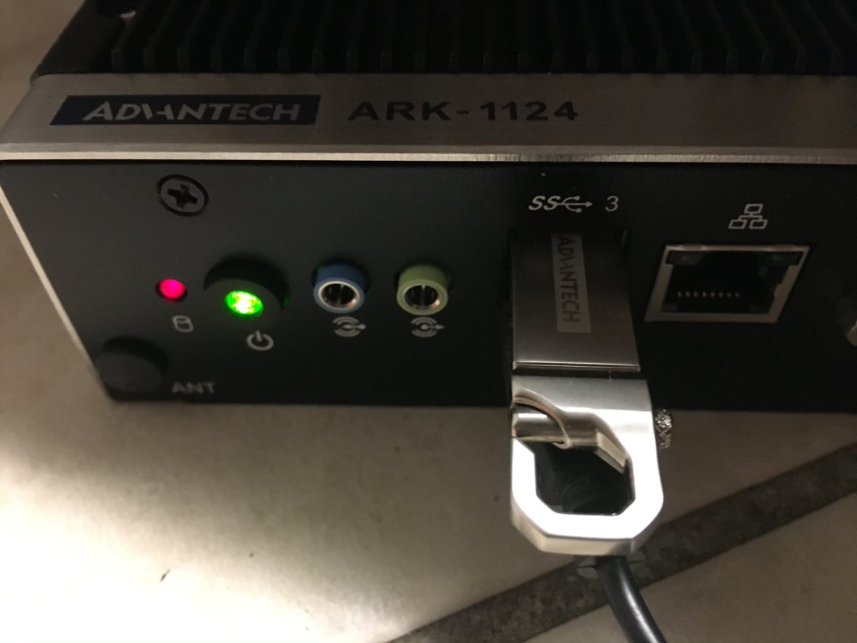
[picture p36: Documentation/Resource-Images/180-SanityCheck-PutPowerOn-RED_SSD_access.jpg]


THE END

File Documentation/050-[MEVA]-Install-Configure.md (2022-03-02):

**Installation of the Open Source Operating System : Linux Ubuntu 18.04 LTS ou 20.04 LTS (Focal Fossa)**

Many IoT Edge computing could do the job : 
* HPE EL300 that is a monster !
* Arestech (another massive monster! as detailed below)
  * MEVA 3110 : https://www.arestech.com.tw/machine-vision-computer-meva-3110.html
    * Factory Automation
    * Vision
    * Inspection
    * Control
    * Surveillance
 
  * Supports 8th/9th Gen Intel® LGA 1151 Processors
    Triple Display Supported by VGA, DVI and Display Port
    2 x DDR4 2400 / 2666MHz SO-DIMM, Max up to 64GB
    3 x Intel GbE Ports, Supporting Wake-on-LAN and PXE
    4 x Removable 2.5“ SATA HDD bay and
    2 x CFast / mSATA, Supporting RAID 0, 1, 5, 10
    4 x Full-Size Mini-PCIe and 4 x SIM Sockets
    9~48V DC Input with Built-in Ignition Power Control
    -40°C ~ 70°C Wide Temperature Operation

    * CPU : Intel(R) Core(TM) i7-9700TE CPU @ 1.80GHz 8 cores
       * specifications : https://openbenchmarking.org/s/Intel%20Core%20i7-9700TE
    * HDD : 3 x 2TB Samsung SSD 860 PRO 
    * RAM : 64 GB (2x32 GB)

**Installing the OS**
- Prepare a bootable USB
- instert in any of the 8 USB port
- Turn the device on (tiny metallic button) ==> you will arrive in the BIOS ==> Quit the BIOS
- in the GNU GRUB menu, choose "Install Ubuntu" > English (even if we are in French) > Keyboard (choose your layout)
- wifi : choose yours > click "Continue"
- Choose install third parties and Download updates and Normal installation (web browser, utilities, ...) : because it is a demo box. Else : not GUI
- Erase disk and install Ubuntu > choose option "Use LVM with the new Ubuntu installation"
- choose the drive SCSI1 (0,0,0) (sda) - 2.0 TB ATA Samsung SSD 860
  - others are (sdb) and (sdc)
- confirmaton : disk will be used : 
  - Ubuntu   /dev/sda (ext4) 2.0 TB
- Timezone : paris
- identification of the computer 
  - your name : admfactoviaone
  - your computers name : iotedge
  - pick a username = admfactoviaone
  - Password : (make your own)
  -  Log in automatically
- wait 2 minutes > reboot > in the menu choose "Ubuntu"
- configure wizzard > "No, don't send system info"
-

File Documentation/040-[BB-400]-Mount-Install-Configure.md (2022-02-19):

# How to mount power, Install and Configure a BB-400

**FIRST SECTION** : Properties of this documentation
* **Difficulty** : 3/5 
  * Detail the difficulty for a non-expert person (not the expert that could do that in 5 minutes) 

* **Estimated time to perform** : 1 hour
  * Gives an estimated time to complete the opetations for a non-expert person (not the expert that could do that in 5 minutes)

**SECOND SECTION**
* Bill of material
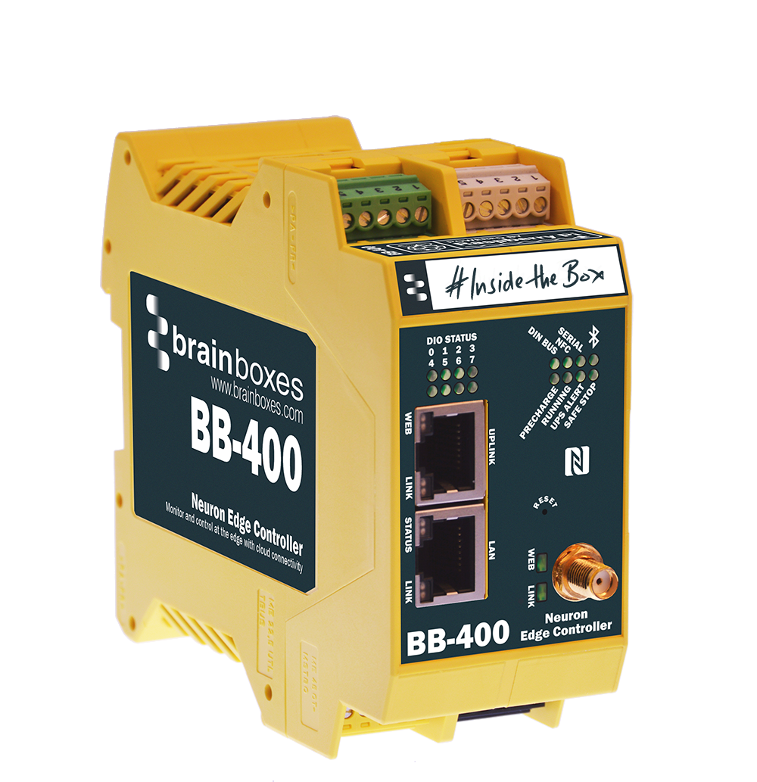
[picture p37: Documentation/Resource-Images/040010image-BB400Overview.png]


https://www.brainboxes.com/news/introducing-the-bb-400-neuron-edge-controller

**POWER**
The recommanded Power Supply is this one (PW-400 : OUTPUT: 12V DC 1.5A) : 
https://www.brainboxes.com/product/accessories/power-supplies/pw-400

However, depending on the Use Case that we want to implement in FactoVia One, we will be needing either 29V DC, 25V DC, 19V DC, 12V DC ou 5V DC.
In this example, we are going to use a 19V DC 3.16A which could be dangerous for the BB-400, that can cope with 15 W Maximum. Else you could grill your BB-400, if we don't take care of what we are plugging on the BB-400 as output devices. 

**Properties** Power Input : +5V to +30V DC 15W Max

Depending on the hardware configuration that you install on the FactoVia One, the calculations below will be different.
In our case, we rely on a 24V DC (eg TowerLights, fans, ...) we have : 
15W / 24V = 0.625 ampers = 625 mA as a MAXIMUM ALLOWED consumption of current (Ampers) for the BB-400.

We mesured previously that the TowerLights (Green/Orange/Red) uses about 21.5 mA. Let's round it up we a security factor to 30 mA per light. But we will not use all the light at the same time.

IMPORTANT : calculation of maximum Ampers and Watts that flow inside the BB-400.
The Max allowed 625 mA (see previous calculation)

We have than Ampers usage for BB-400 + TowerLights + horn + fan ... that should be less than 150 mA, i.e. that are in total far less than 625 mA. As a result, we are secured !

# INSTALL
# NETWORK CONFIGURATION
Below, we are going to use the NETGEAR Switch : 
- prerequisite : Plug in the RJ45 of ARK1124 to NETGEAR Switch (for instance entry "1")
- Plug in the RJ45 of BB-400 (the entry "LAN") to NETGEAR Switch (for instance entry "2")

Notes : 
1) Alternative to For debug purpose, you could directly plug-in a RJ45 ethernet cable between the BB-400 (LAN and not UPLINK for this debug configuration) and ARK-1124 (either female front plug or rear).
2) You could also use wifi access

**SANITY CHECK**
* Test the output (for example green pins 1 and 3) using a Multimeter : when plugging a LED on an output, we have 4.5V, 20 mA
* go to the BB-400 management portal at the URL : https://bb400-XXXX:9090 (where XXXX is the last 4 digit of your MAC address)
* Query the BB-400 REST API at the URL (not https): http://bb400-XXXX:9000/io 
it should return the status of the LED in front of the BB-400
* From the ARK-1124 :  
  *  ping bb400-XXXX
     *  should return a time<1ms and an IPv6 address
  *  ping bb400-XXXX -4  // to force returning the IP in v4
     *  should return a time<1ms and an IPv4 address
     *  IPv4 = 192.168.127.1
*  Now we know its IPv4 address, we could test the web portal https://192.168.127.1:9090/io
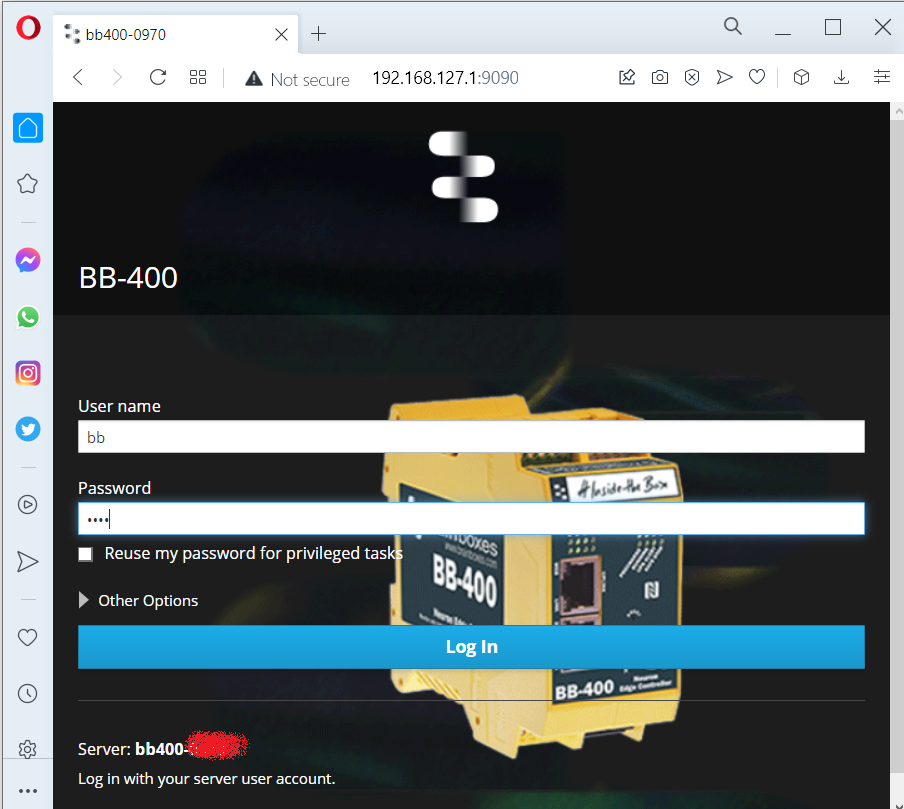
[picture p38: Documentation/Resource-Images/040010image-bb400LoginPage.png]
     *    
*  and the REST API using its URL : http://192.168.127.1:9000/io
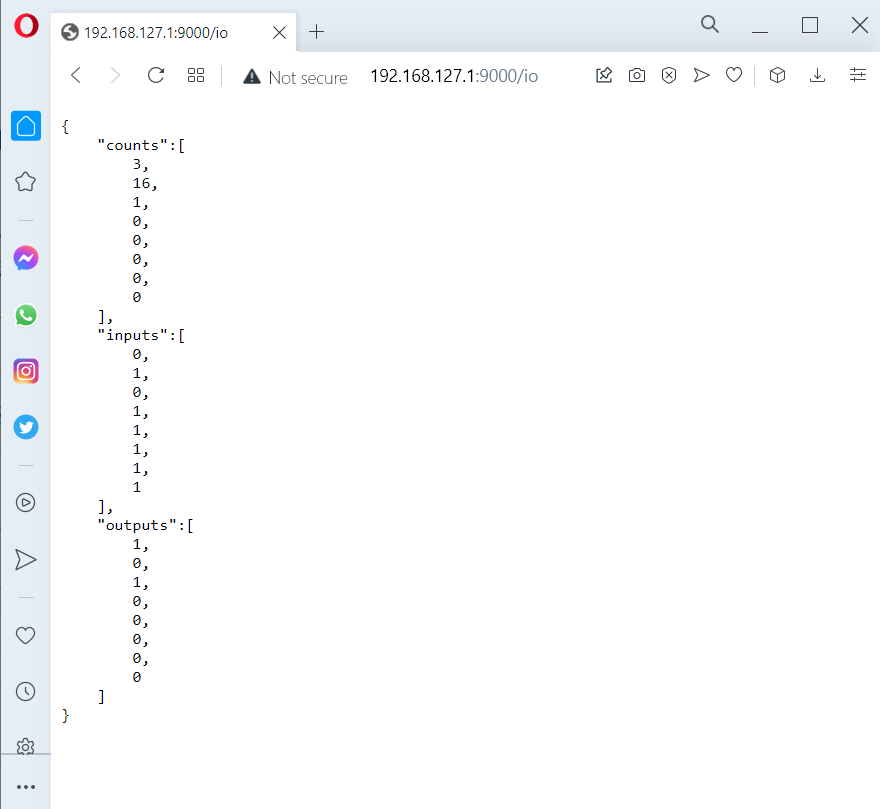
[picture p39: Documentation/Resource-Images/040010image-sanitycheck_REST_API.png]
   *

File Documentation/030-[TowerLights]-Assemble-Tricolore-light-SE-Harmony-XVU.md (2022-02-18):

* We are going to use an equipment that is designed to be Green

* Before you start : 
  - look at this 50 sec video from Schneider Electric : https://www.youtube.com/watch?v=KaQS2MfXHi4
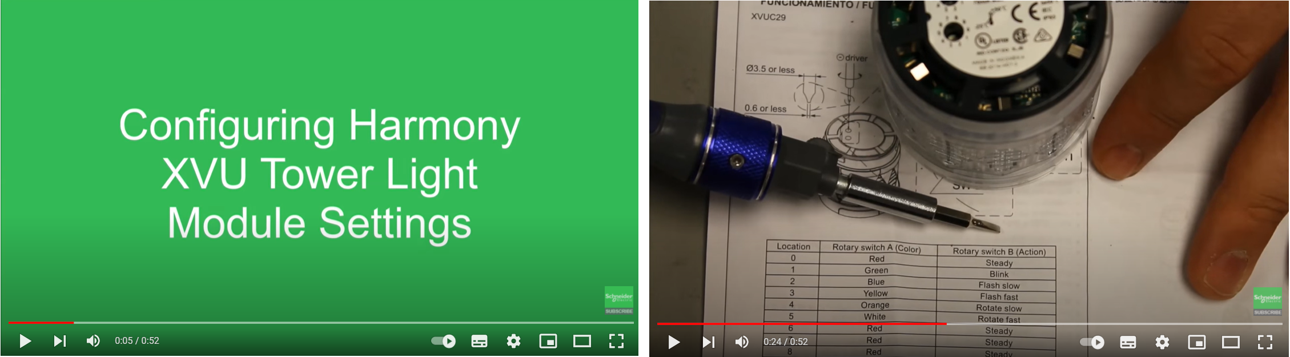
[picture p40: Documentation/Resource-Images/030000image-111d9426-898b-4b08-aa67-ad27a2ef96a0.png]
    
  - https://youtu.be/FKZX43fe-6s 
  - https://youtu.be/6PTkboC0bvQ 
  - get 1 to 6 wires (according to the modules you want to use). They should at least be 150 cm long
  - **/!\ NEEDS A FUSE !!!  Capacity 0.5 A, 125 V**
  - get a fuse support : 
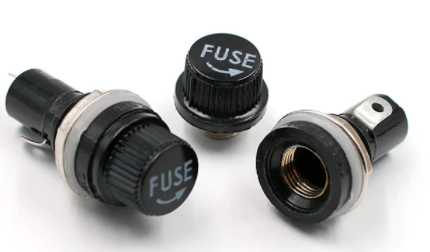
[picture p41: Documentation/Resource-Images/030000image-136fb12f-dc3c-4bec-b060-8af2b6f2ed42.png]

   or for our tests : 
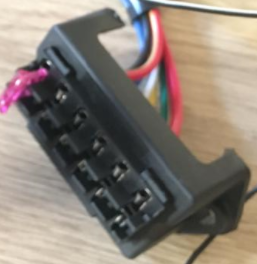
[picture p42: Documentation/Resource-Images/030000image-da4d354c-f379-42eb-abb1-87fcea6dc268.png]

* unpack the puzzle !
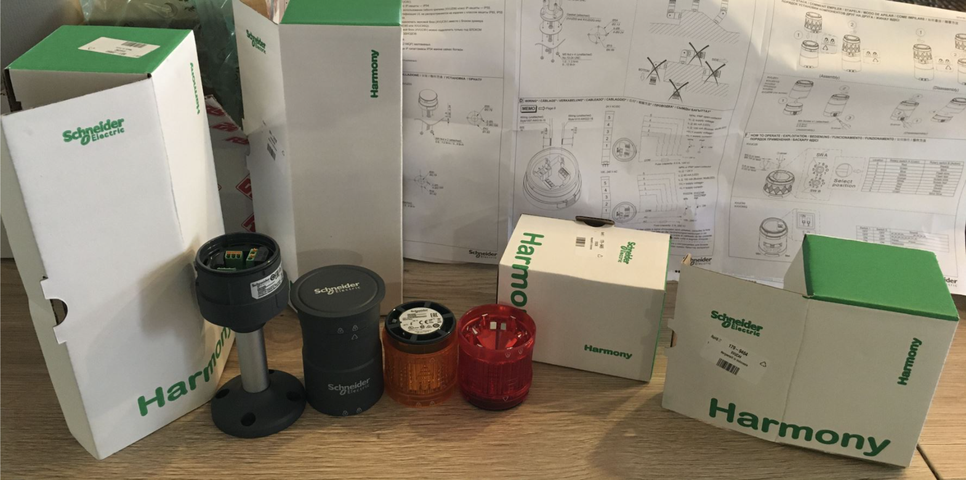
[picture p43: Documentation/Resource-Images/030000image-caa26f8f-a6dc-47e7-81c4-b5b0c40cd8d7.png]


* Perform the wiring according to the documentation ; **DON'T FORGET to add a FUSE that is not provided**.
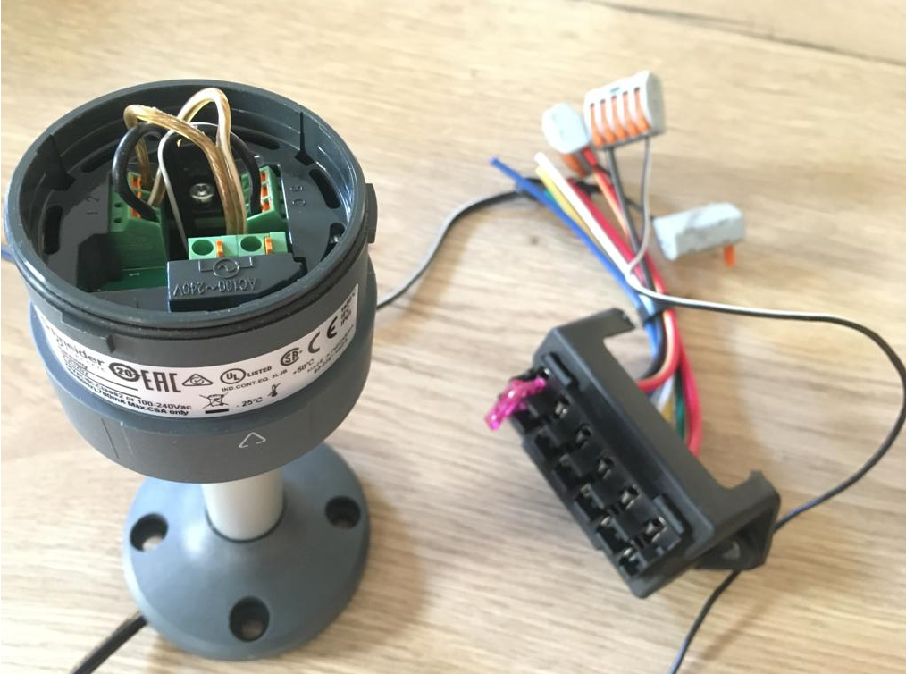
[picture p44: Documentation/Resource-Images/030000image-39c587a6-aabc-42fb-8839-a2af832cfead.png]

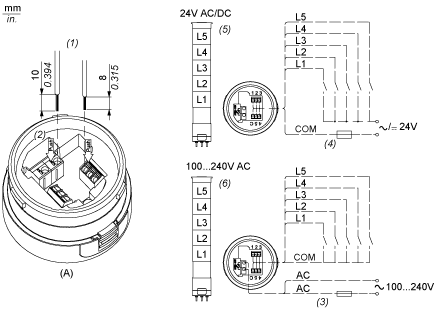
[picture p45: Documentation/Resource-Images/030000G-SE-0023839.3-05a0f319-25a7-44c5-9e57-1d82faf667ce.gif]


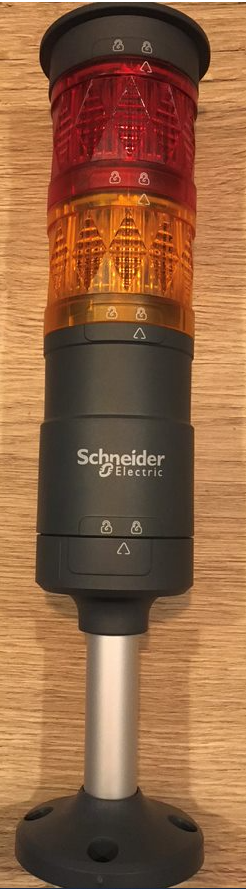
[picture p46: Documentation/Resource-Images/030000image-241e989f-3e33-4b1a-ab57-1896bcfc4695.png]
* Assemble all the modules according to this detailed image (security lock on the base, via a small screw, has to be removed or untightened first. See video in the link below). It will look like this : 
more info in video : https://youtu.be/ZfthcWQhHGk

SANITY CHECK : 
* When blinking versus no blinking, we have the current intensity consumption of 21.5 mA versus 12 mA (the images below could lead to error, because we have a lag between the multi-meter that mesures the data and displays it, the actual blink and the remanescence effect of the light, and the time the camara takes a picture !)
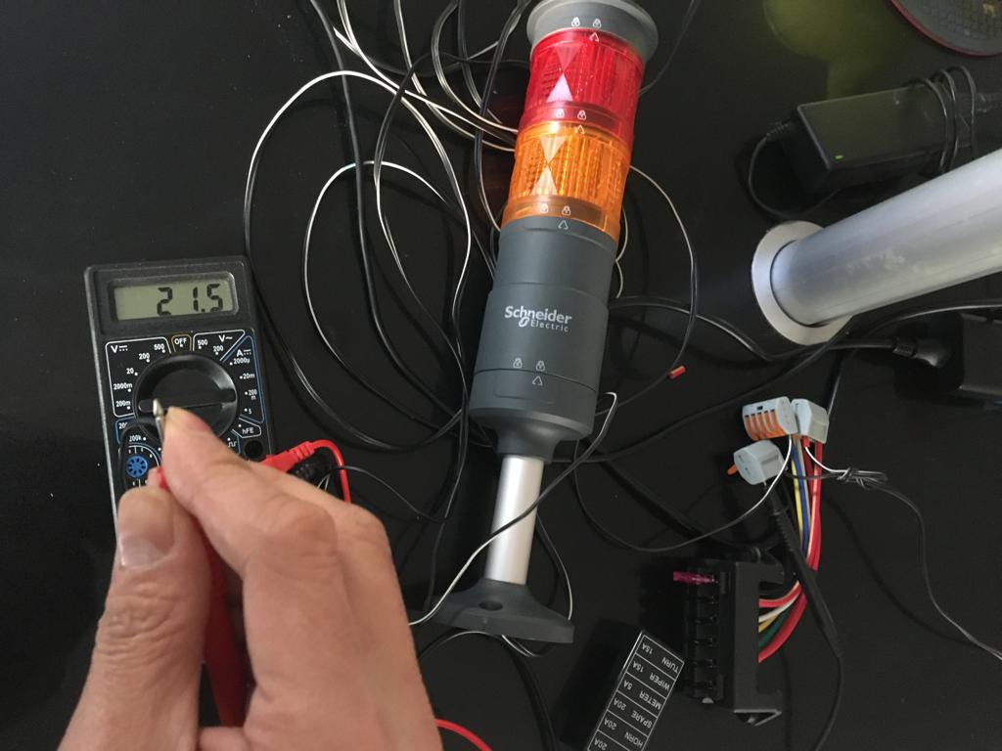
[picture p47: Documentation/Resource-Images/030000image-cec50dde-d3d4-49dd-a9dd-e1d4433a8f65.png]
* 
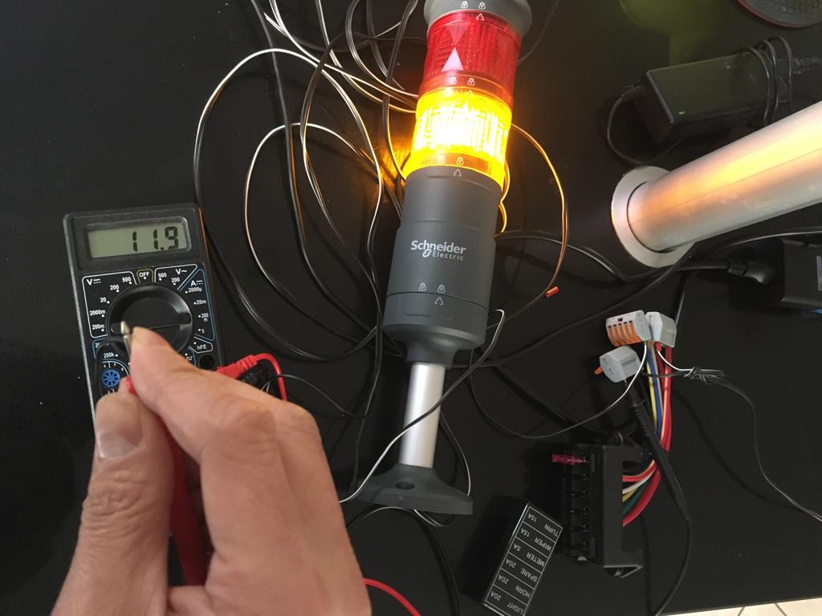
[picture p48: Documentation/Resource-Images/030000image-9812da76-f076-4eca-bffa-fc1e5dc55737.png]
*

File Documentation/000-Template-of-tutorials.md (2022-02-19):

# Template of tutorials in this repository
In order to follow a similar structure of tutorials, we are using the  instructions template as a guidance

**File name**
* namename naming convention  
  * [3 digits identification]-{name of the element within the mini-factory}{summary of the operations that are detailed, words are separated by dash}.{markdown file extension}
  * [010]-[ARK1124]-Assemble-SSD-&-RAM.md

**FIRST SECTION** : Properties of this documentation
* **Difficulty** : 
  * Detail the difficulty for a non-expert person (not the expert that could do that in 5 minutes) 

* **Estimated time to perform** : 
  * Gives an estimated time to complete the opetations for a non-expert person (not the expert that could do that in 5 minutes)
**SECOND SECTION**
* Bill of material

**OTHER VARIOUS SECTIONS**
* Descrption of the other steps 

**LAST SECTION**
* Sanity check : end with a sanity check to ensure that what you have got is working properly

**Option** : 
* troubleshoot : description of errors and how to fix it if applicable

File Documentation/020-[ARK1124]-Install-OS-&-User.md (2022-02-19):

# OS not Open Sourced : Install Windows 10 & Configure ADVANTECH ARK-1124

**FIRST SECTION** : Properties of this documentation
* **Difficulty** : Low (1/5)
  * Detail the difficulty for a non-expert person (not the expert that could do that in 5 minutes) 

* **Estimated time to perform** : 1 hour 
  * Gives an estimated time to complete the opetations for a non-expert person (not the expert that could do that in 5 minutes)

**SECOND SECTION**
* Bill of material
  * NETGEAR Switch 
  * ARK-1124

**THIRD SECTION : install Windows 10**
For the demo purposes, you could use the user / password : 
* user : admfactoviaone
* password : demo-opensource-factovia-2022-industry

* Prepare USB Key > 5 GB
* Download special Microsoft tool **"MediaCreationTool21H2.exe"** to prepare the USB Key in 1 click (download latest version, and write simultaneously in the USB Key)

* and run the tool (see on the right)
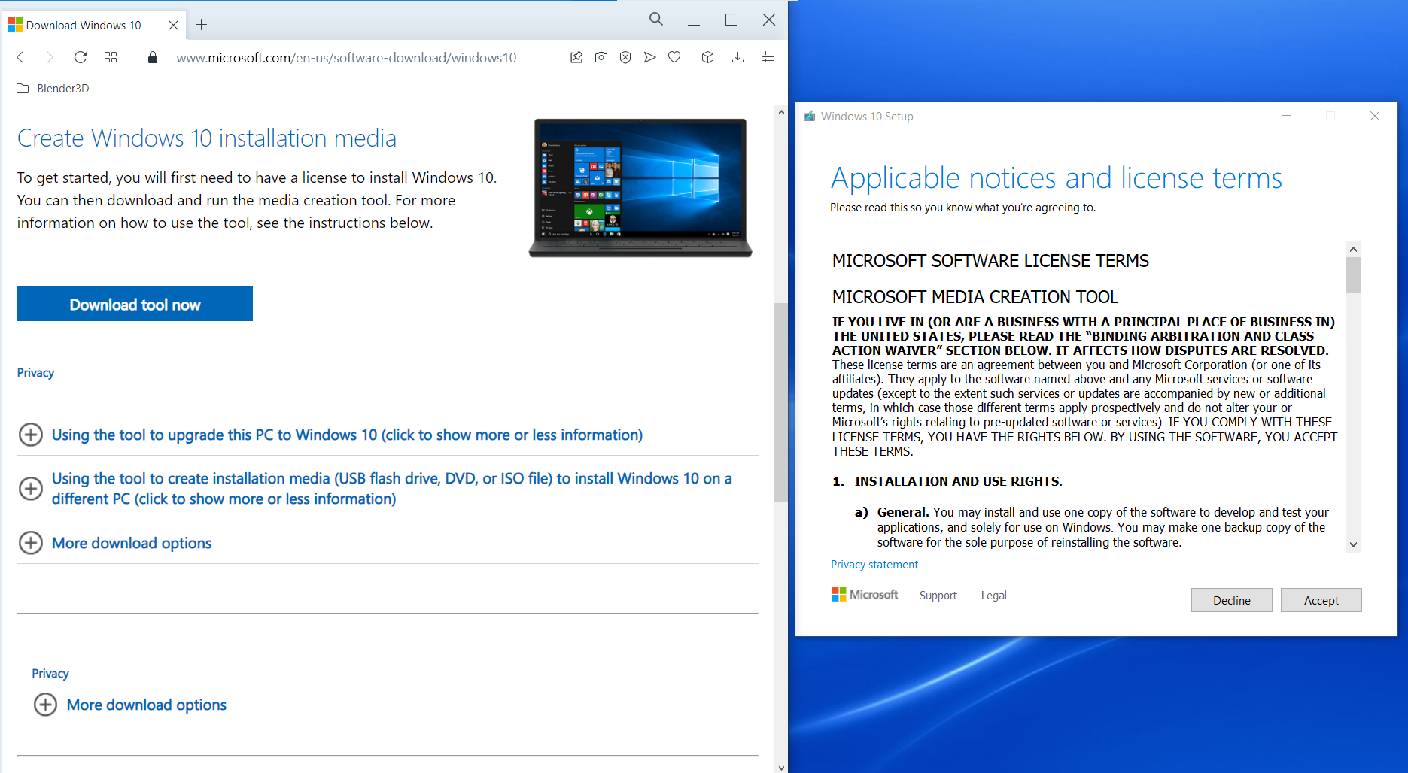
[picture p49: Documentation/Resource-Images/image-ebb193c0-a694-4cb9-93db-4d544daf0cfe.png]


* insert the USB Key and boot. It will start the basic mini-install
* when asked to enter the registration Key, choose "I don't have the registration key"
  Then it will lead you to a menu to choose which version of Win 10 to use. 
  Because it is a demo version for FactoVia One, choose "Windows 10 Education x64"
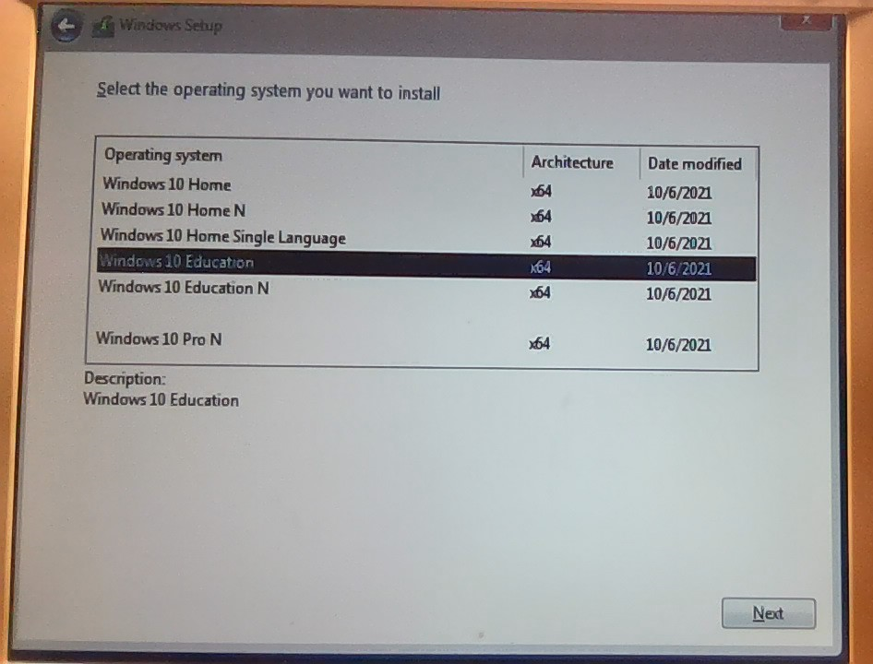
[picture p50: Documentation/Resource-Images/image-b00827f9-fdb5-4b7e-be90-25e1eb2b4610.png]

* prepare you license key (usually choose "Windows 10 for Education - MultipleActivation"
  for example : KBKGK-XXXXX-XXXXX-XXXXX-XXXXX
* accept the terms & conditions
* to choose a completely new install on the 59.6GB of free storage SSD, simply press "Next"
* the Install process will start (copying Windows files, getting files ready for installation, installing features, installing updates, finishing up)

* choose for the login "Joint domain" > user : see above > password : see above  > question 1 : "pet 1 name" = cat > "city born" = cat > "child nickname" = cat
* PRIVACY : No (location) > No (Find device) > "send required diag data" > No > No > Cortana = "Not now" ...

# NETWORK CONFIGURATION
Below, we are going to use the NETGEAR Switch : 
- Plug in the RJ45 of ARK1124 to NETGEAR Switch (for instance entry "1")

Windows 10 is tricky to configure the IP Address of the ARK1124 and often leads to the error *"Can’t save IP settings. Check one or more settings and try again."*.
Let's use the old fashion way (see : https://www.thewindowsclub.com/cant-save-ip-settings-windows)

You can follow the given steps to change IP Settings by Control Panel.

Trick with old fashion way with old Windows menus : Open Control Panel from the Start Menu.
Make sure your “View by” is set to Large icons.
Click Network and Sharing Center > Change adapter settings.
Right-click on your Ethernet connection and select Properties.
Select Internet Protocol Version 4 (TCP/IPv4) and click Properties.
Now, select “Use the following IP address”, insert the IP address, Subnet Mask, Default Gateway, DNS Server, and click OK. Then, we will in the information :  
- IP address  = 192.168.127.3
- Subnet Mask = 255.255.255.0
- Default Gateway = {leave it blank}
- DNS Server      = {leave it blank}

Note : Now if we use the new Windows 10 menus to access a similar information, we have : 
- IP settings = Manual
- IP address = 192.168.127.3
- Subnet prefix lenght = 24 
- Prefered  DNS = {leave it blank} 
- Alternate DNS = {leave it blank}

Then Windows indicates : 
- IPv4 gateway     = 192.168.127.1
- IPv4 DNS servers = 192.168.24.254 

 **SANITY CHECK :**



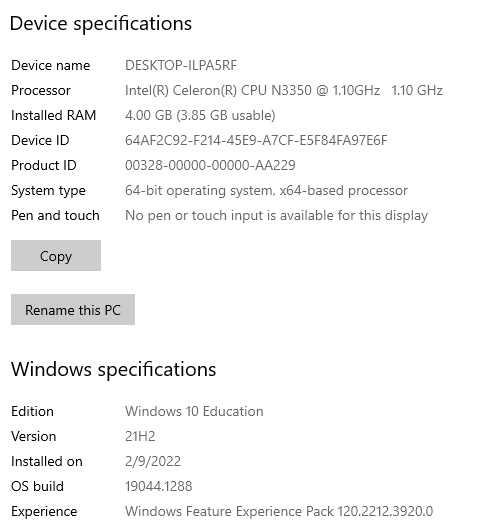
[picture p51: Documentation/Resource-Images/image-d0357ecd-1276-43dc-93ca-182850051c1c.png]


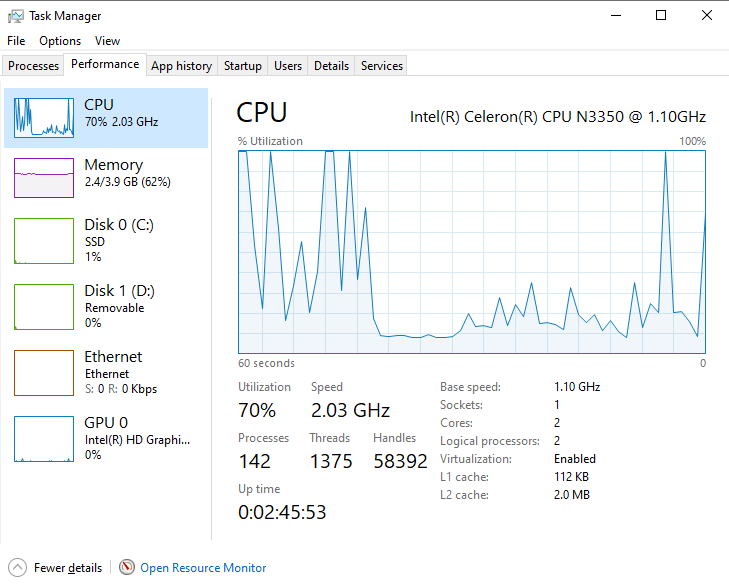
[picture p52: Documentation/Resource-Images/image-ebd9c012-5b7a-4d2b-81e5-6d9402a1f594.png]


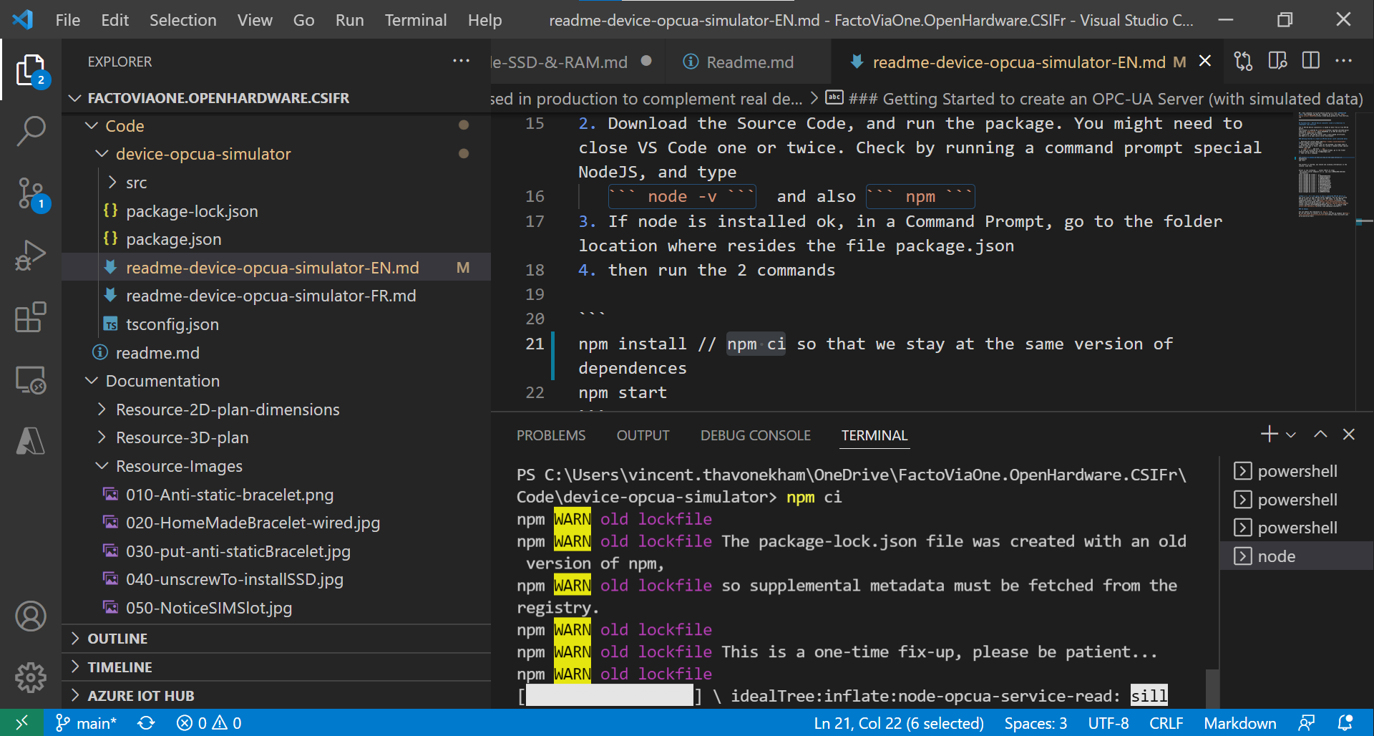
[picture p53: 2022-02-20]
Code/device-opcua-simulator/Resources-Images/010-img-installPackage.png

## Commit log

2022-02-15 Add FactoVia One & 2 OpenSource logos (h/w & s/w)
    FR: Ajout de l'image d'introduction de FactoVia One avec les 2 logos OpenSource (matériel et logiciel)
    EN: Add splash screen of FactoVia One and 2 OpenSource logos (hardware & software)
2022-02-15 Add license
    FR : Ajout licence "OSHW – OpenSource Hardware"
    EN : Add "OSHW – OpenSource Hardware" license
2022-02-15 remove Markdown bold format
    FR: retour le format Markdown de Gras
    EN : remove Markdown bold format
2022-02-16 add Tower Light Green/Orange/Red (Schneider Electric) assemble instructions
2022-02-16 add Bill of Material
2022-02-18 Corrected missing drawing frame
2022-02-18 rename images folder, and add doc for IoTEdge box
    [FactoViaOne_CAD_3D_Copyright_(C)2022_OSHW_Vincent_Thavonekham.stl]
2022-02-19 Rename 030-TowerLights-Assemble-your-Schneider-Electric-Harmony-XVU.md to 030-[TowerLights]-Assemble-Schneider-Electric-Harmony-XVU.md
    put into proper naming convention to be similar as the other ones
2022-02-21 rename license
    [FactoViaOne_CAD_3D_LicenseOSHW_Attribution_Vincent_Thavonekham.stl]
2022-02-21 add Bill of material v0
2022-03-02 add mini-robot arm sizes
2022-03-07 Adds a Blender model of the factory with working textures.
    [FactoryModel.blend]
2022-03-13 Adding NR UR Robot
    Spécifications
    height = 165 mm
    length = 185 mm
    width = 85 mm
    [NR UR Type 1.stl, tinker.obj]
2022-03-13 rename files
    [Mini-robotarm-NR-UR-Model1.obj]
2022-03-14 Add 3D printing info
    [Mini-robotarm-NR-UR-Model1_scale80.blend, Mini-robotarm-NR-UR-Model1_scale80.obj]
2022-03-14 Add robot arm to Blender of main mini-factory
    [FactoryModel.blend, Mini-robotarm-NR-UR-Model1_scale80.blend]
2022-03-14 update camera viewport. Rename 3D rendering
2023-07-10 Update 010-[ARK1124]-Assemble-SSD-&-RAM.md
    Add update while assembling two other ARK-1124
